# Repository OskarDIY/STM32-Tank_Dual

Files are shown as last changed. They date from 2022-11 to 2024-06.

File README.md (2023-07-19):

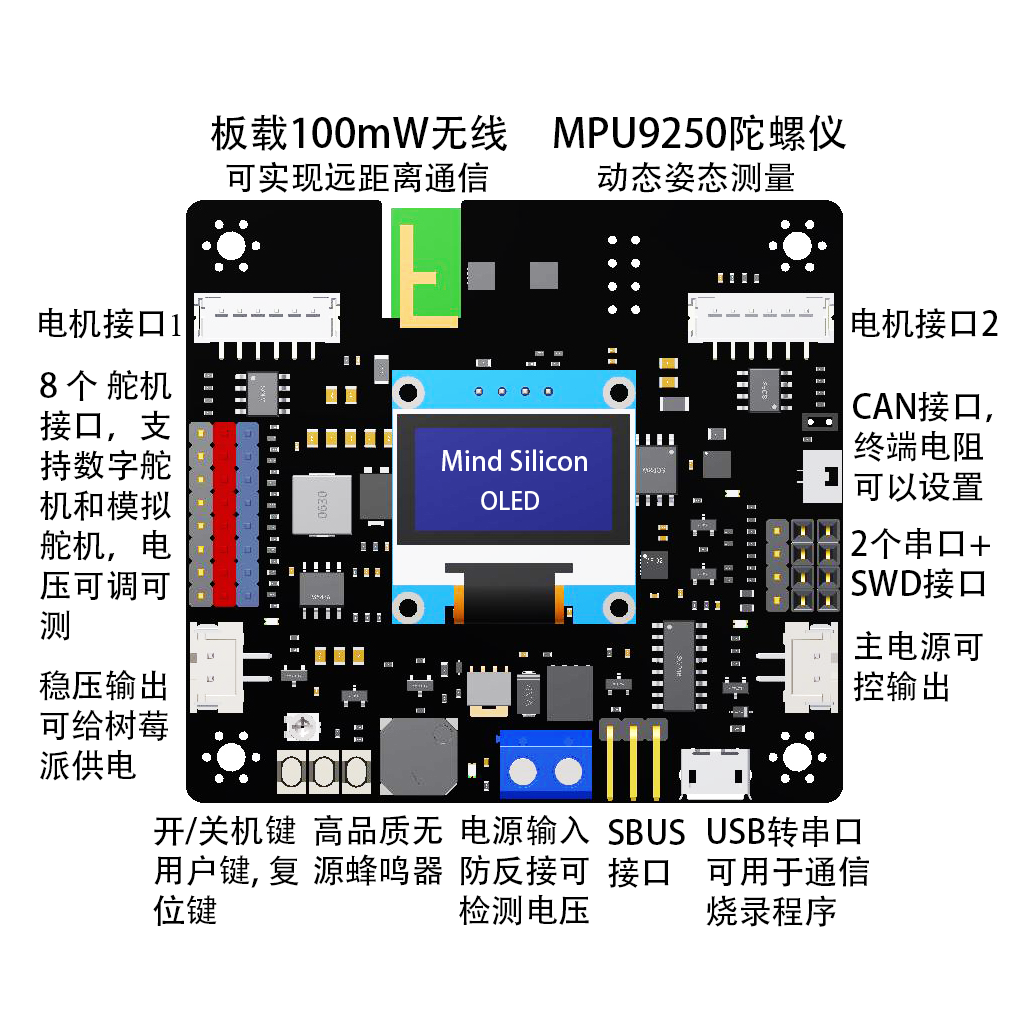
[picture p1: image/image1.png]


Tank Dual开发板是一款专门为机器人项目开发的STM32多功能控制板，可以同时控制8个舵机和2个编码电机，板载MPU9250姿态传感器，自带100mW无线可实现远距离遥控、通信，支持CAN通信，USB烧录/通信，串口通信等。稳压输出可以对外给树莓派供电，控制外部负载。  
主控：STM32F103RCT6，72MHz，ARM-Cortex M3内核，主流学习平台。  
无线：板载100mW无线模块，频段2.4GHz，可设置地址和频道。自带PCB天线距离轻松超过200米，可接外置天线距离可达500米，可本店手柄配套使用。  
9轴传感器：MPU9250（3轴陀螺仪+3轴加速度+3轴磁力计）  
舵机接口：8路硬件PWM舵机接口，5A大电流稳压芯片，可调电压。  
电机接口：2路直流有刷电机接口，支持正交编码器，每路3A大电流，支持12/24V电机。  
OLED屏幕：0.96寸OLED，可以显示信息，播放开关机动画。  
USB转串口：板载1路USB转串口电路，可以与电脑或树莓派USB通信，可以通过USB烧录程序。  
串口：2路串口（1路可以用作SBUS，与航模SBUS接收机通信）。  
CAN通信：1路CAN接口（带跳线电阻）。  
存储：板载W25Q64闪存芯片，内置文件系统，方便保存数据。  
声光提示：无源蜂鸣器，可以播放音乐，1路系统LED，3路电源LED。  
按键：开机/关机键，复位键，1个用户自定义按键。  
电源输入：6～24V供电，支持对外3A可控输出，可测量电压。  
稳压输出：支持对外3A稳压输出，与舵机共用稳压电源，开关可控，可测量电压，可以给树莓派供电。（舵机和稳压输出总和不可超过5A）。  
调试接口：SWD接口。  

说明：项目开发者在2023年5月发布了新版本的硬件，接口和外观跟原来的板子完全一致，STM32单片机的IO口分配和之前略有变化，更加优化和完善，代码和原理图也在2023年5月28日重新上传了。如果您手上用的是之前早期版本的硬件，因为硬件原理的改变，新的代码将不再适用，您可以私信开发者获取早期版本的资料，感谢您的理解！

 **项目开发工具为：STM32CubeIDE，可自行在ST官网下载安装。** 

原理图和源码的相关讲解可以在B站查看，https://space.bilibili.com/375400171/video

开发板购买链接，https://item.taobao.com/item.htm?spm=a230r.7195193.1997079397.6.b6c05627CU6ucV&id=565040857054&abbucket=20

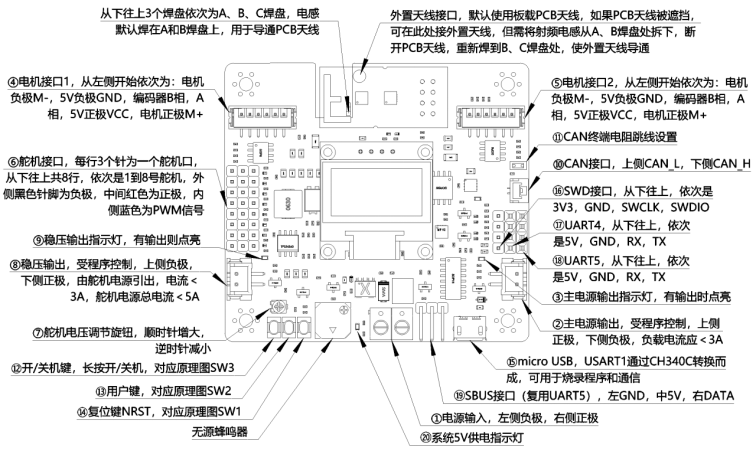
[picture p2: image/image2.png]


上图中需要注意的是：  
⑫开/关机键，长按可以开/关机，对应原理图SW3。在USB和主电源同时供电时，程序会自动运行，但仍需通过按键开机后主电源才会启动，电机和舵机才会得到电力供应。  
⑬用户键，对应原理图SW2，可通过程序来实现自定义功能。  
⑭复位键NRST，对应原理图SW1，按下后使STM32复位。程序执行异常，或者通过SWD下载程序出错时可以尝试通过复位排除问题。  
①主电源接口为整个系统的供电接口，左侧负极，右侧正极，支持2~6S电池输入。  
②主电源输出口电压与主电源接口输入电压相同，接口类型为XH2.54-2P，上侧正极，下侧负极，负载电流应＜3A，输出受程序控制。只能输出，不可用于输入。  
③主电源输出指示灯，当主电源输出口有输出时点亮。  
④⑤电机接口为PH2.0-6P接口，线序为M-、5V-、B、A、VCC、M+，在连结电机时请确保线序正确。电机驱动电压与主电源接口输入电压相同。  
⑥舵机接口，每行3个针为一个舵机口，从下往上共8行，依次是1到8号舵机，外侧黑色针脚为负极，中间红色为正极，内侧蓝色为PWM信号。为了匹配不同电压规格的舵机，舵机口的电压是可以通过⑦调节的。  
⑦电压调节旋钮，可以调节⑥舵机接口和⑧稳压输出电压，顺时针增大，逆时针减小。
⑧稳压输出接口，接口类型为XH2.54-2P，输出受程序控制，上侧负极，下侧正极。负载电流应＜3A，可以用于给树莓派供电。由于稳压输出是从舵机电源中引出，它的电压同样受⑦控制，且和舵机电源总电流应＜5A。给树莓派供电时，请务必注意使稳压输出电压≤5V，且确认好正、负极接线正确，否则将烧坏树莓派。  
⑨稳压输出指示灯，当稳压输出口有输出时点亮。  
⑩CAN接口，接口类型为GH1.25-2P，上侧CAN_L，下侧CAN_H。  
⑪CAN终端电阻跳线设置，跳线帽为2.0毫米规格。  
⑮micro USB，USART1通过CH340C转换而成，可用于烧录程序和通信。当无法通过SWD下载程序时，也可以通过USB下载程序。  
⑯SWD接口，从下往上，依次是3V3，GND，SWCLK，SWDIO。此处的3V3即3.3V，只可用于编程器烧录，不可对外供电。  
⑰UART4，从下往上，依次是5V，GND，RX，TX，此处的5V外接负载电流应＜50mA。  
⑱UART5，从下往上，依次是5V，GND，RX，TX，此处的5V外接负载电流应＜50mA。  
⑲SBUS接口（复用UART5），左GND，中5V，右DATA，此处的5V外接负载电流应＜50mA。  
⑳系统5V供电指示灯。  

2.2无线介绍  
无线发射功率100mW，频段2400 ~ 2525MHz。  
可通过上位机软件设置无线地址和频道，见下文。  

3、注意事项  
控制板可以通过SWD接口或USB接口烧录程序，SWD烧录速度快且支持调试，USB接口可以在没有编程器（ST-Link或JLink）的情况下完成烧录工作。  
SWD烧录可以直接在Keil中完成，烧录时需要通过USB供电，如果用主电源供电，则需要按住开机键不要松开。  
SWD烧录中，如果Keil提示内部异常、内部错误，一般是由于STM32没有响应编程器的复位指令，需要手动按住板子上的复位键，同时点击Keil中的下载按钮（或者按下F8），然后迅速松开复位键，程序即可下载到芯片中。  
开/关机动画保存在外置Flash芯片W25Q64中，不会因为重新烧录程序而丢失。格式化外置Flash芯片或者删除芯片中的资源文件，将导致开/关机动画丢失，但不会影响其他功能。  

4、通信协议  
4.1通信数据格式  
该通信协议适用于手柄、控制板和上位机三者之间的通信。手柄，接收机，上位机软件，受控设备之间，所有通信内容均用16进制表示，小端模式（低字节在前，高字节在后），单次通信数据长度不可超过32字节。  
格式：帧头 + 通信代码 + 帧长度 + 数据 + 校验  
其中具体含义为：  
帧头：2字节，固定为0xAAAA，用于表示一次通信的开始，或者区分不同数据帧。  
通信代码：1字节，用来区分通信的类型，详见表4.1。  
帧长度：1字节，本次通信数据帧长度，指包含帧头、通信代码、帧长度、数据和校验在内的总长度。  
数据：若干字节，数据载荷，长度可变。  
校验：16位CRC校验值，MODBUS格式。详见表4.2。  
表4.1	通信代码说明  
通信代码	说明  
0x01	遥控指令，这是一条从手柄发往接收机的指令。手柄通过这条指令将摇杆、按键、手柄电量在内的所有信息发送给接收机，接收机再通过串口输出。发送频率为200Hz。  
0x09	反馈指令，这是一条从接收机发往手柄的指令，用来触发手柄震动。用户通过接收机的串口把这条指令发送给接收机，然后接收机通过无线发送给手柄，手柄发出震动。没有发送频率限制，用户可以根据需要去触发手柄震动。  
0x15	下行透传指令，上位机通过USB把指令发送给手柄，手柄将指令发送给接收机，然后接收机通过串口输出。注意：长度不可以超过26字节。  
0x16	上位机发送指令给控制板，设置8个舵机的PWM值和电机转速值，使能稳压输出和主电源输出。此指令会启动内部PID调速算法，请确保电机霍尔编码器正常。  
0x1D	上行透传指令，用户通过接收机的串口把这条指令发送给接收机，然后接收机通过无线发送给手柄，手柄通过USB接口输出该指令。注意：长度不可以超过26字节。  

表4.2	CRC算法说明  
CRC算法	多项式公式	宽度	多项式	初始值	异或值	输入反转	输出反转  
MODBUS	x16 + x15 + x2 + 1	16	8005	0xFFFF	0x0000	true	true  
CRC算法的参考程序，见例程或校准软件。CRC16计算页面链接（注意选MODBUS算法）http://www.ip33.com/crc.html  

4.2通信示例  
0x01指令：该指令是所有指令中最重要的指令，只有理解它的含义，才可以弄清楚手柄是如何控制其他设备的。指令中所有数据均为16进制，下边给出0x01指令的具体示例：  
示例：AA AA 01 0D DF 7F 7F 7F 7F 00 00 D7 51  
第1、2字节0xAA，0xAA为帧头，标志着一帧数据的开始。  
第3字节0x01为命令代码。  
第4字节0x0D为帧长度，这条指令长度为13个字节，用16进制表示就是0x0D。  
第5字节0xDF表示手柄电池此时的电压，计算公式：（0xDF +200）÷100=4.23V，此时手柄电池电压为4.23V，其它值时以此类推。手柄低电量提醒电压为3.8V，自动关机电压为3.75V。
第6字节为模拟通道1，对应手柄左侧摇杆的水平方向，取值范围为0x00~0xFF，中值为0x7F。摇杆往左打极限值为0xFF，往右打极限值为0x00。
第7字节为模拟通道2，对应手柄左侧摇杆的垂直方向，取值范围为0x00~0xFF，中值为0x7F。摇杆往下打极限值为0xFF，往上打极限值为0x00。
第8字节为模拟通道3，对应手柄右侧摇杆的水平方向，取值范围为0x00~0xFF，中值为0x7F。摇杆往左打极限值为0xFF，往右打极限值为0x00。
第9字节为模拟通道4，对应手柄右侧摇杆的垂直方向，取值范围为0x00~0xFF，中值为0x7F。摇杆往下打极限值为0xFF，往上打极限值为0x00。
第10、11字节，这两个字总共16位，对应手柄的16个通道。从最高位第16位到第1位，依次是：L2、L1、LU、LL、LD、LR、SE、ST、RL、RD、RR、RU、R1、R2、R-KEY、L-KEY。其中R-KEY和L-KEY为摇杆往下按对应的按键。
第12、13字节为校验值，计算前11个字节的CRC16校验值得到0x51D7，按照小端模式，低字节0xD7，高字节0x51依次排列。

0x09指令：接收机发往该指令给手柄，用于触发手柄震动。
示例：AA AA 09 07 01 0E 32
第1、2字节0xAA，0xAA为帧头，标志着一帧数据的开始。
第3字节0x09为命令代码。
第4字节0x07为帧长度，这条指令长度为7个字节。
第5字节0x01表示触发手柄左侧电机振动，如果要触发邮册电机则应为0x02。该字节只能取0x01或者0x02。
第6、7字节为校验值，计算前5个字节的CRC16校验值得到0x320E，按照小端模式，低字节0x0E，高字节0x32依次排列。

0x15指令：上位机通过手柄透传给接收机的数据，然后通过接收机输出给STM32进行处理。
示例：AA AA 15 07 00 0E 34
第1、2字节0xAA，0xAA为帧头，标志着一帧数据的开始。
第3字节0x15为命令代码。
第4字节0x07为帧长度，这条指令长度为7个字节。
第5字节0x00上位机发出的数据，字节长度可变，但不可超过26字节。因为一次通信最多发送32字节数据，其他部分已占据6字节。
第6、7字节为校验值，计算前5个字节的CRC16校验值得到0x340E，按照小端模式，低字节0x0E，高字节0x34依次排列。
可以通过这条指令来模拟手柄向开发板发送的数据，格式参照0x01指令。可以用于实现上位机通过控制板的USB口向控制板发送指令数据，控制板像响应手柄指令一样做出相同响应，具体实现由用户决定。

0x16指令：上位机发送指令给控制板，设置8个舵机的PWM值和电机转速值，启动稳压输出和主电源输出。PWM有效范围是500~2500μS，PWM频率为50Hz。每个电机的转速值用2个字节（BYTE1，BYTE2，简写为B1、B2）表示。B1字节的最高2位用来表示：惯性滑行（00）、正转（01）、反转（10）、阻尼刹车（11）。B1字节低6位和B2字节8位共同组成速度值(((B1 & 0x3F)<< 8) | B2)。当B1高2位为正转（01）或者反转（10）时，如果速度值为0则会锁定电机位置，使电机迅速停转并保持不动。电机速度的单位为毫米每秒（mm/s），表示电机转动所产生的线速度。
示例：AA AA 16 1B 00 00 00 00 00 00 00 00 00 00 00 00 00 00 00 00 00 00 00 00 00 5E A6
             舵机：1    2    3    4    5    6    7    8   B1B2 B1B2 PWR
第1、2字节0xAA，0xAA为帧头，标志着一帧数据的开始。
第3字节0x15为命令代码。
第4字节0x1B为帧长度，这条指令长度为27个字节，即十六进制0x1B。
第5 ~ 20字节依次为1至8舵机口的PWM值，每个舵机占用2个字节，注意PWM有效范围是500~2500μS，PWM频率为50Hz。
第21~24字节依次为电机1接口和电机2接口的转速值。每个电机的转速值用2个字节（BYTE1，BYTE2，简写为B1、B2）表示。B1字节的最高2位用来表示：惯性滑行（00）、正转（01）、反转（10）、阻尼刹车（11）。B1字节低6位和B2字节8位共同组成速度值(((B1 & 0x3F)<< 8) | B2)。当B1高2位为正转（01）或者反转（10）时，如果速度值为0则会锁定电机位置，使电机迅速停转并保持不动。电机速度的单位为毫米每秒（mm/s），表示电机转动所产生的线速度。
直流减速电机转速一般在1000RPM（转每分钟）以内，根据电机转速和车轮直径可以算出车轮线速度的合理区间。请注意输入合理的速度值，以免电机过载。需要特别注意的是，此指令会启动内部PID调速算法，请确保电机编码器正常，编码器异常可能导致灾难性后果。
第25字节PWR用于启动稳压输出和主电源输出，0x00表示不启动，0x01表示仅启动舵机电源用于对外提供稳压供电，0x02表示仅启动主电源输出口对外供电，0x03表示同时启动多机电源和主电源。注意启动前务必检查舵机电源和主电源电压，以免烧坏外接设备。另外，请确保系统主电源已经接通且开启，参考2.1章节接开关机操作。
第26、27字节为校验值，计算前25个字节的CRC16校验值得到0xA65E，按照小端模式，低字节0x5E，高字节0xA6依次排列。

0x1E指令：控制板对上位机0x16指令的返回信息，用来返回设置是否成功，以及电机转速、设备姿态、故障信息。
示例：AA AA 1E 11 00 00 00 00 00 00 00 00 00 00 00 7F F6
B1B2 B1B2  R    P    Y
第1、2字节0xAA，0xAA为帧头，标志着一帧数据的开始。
第3字节0x1E为命令代码。
第4字节0x11为帧长度，这条指令长度为17个字节。
第5字节0x00表示设置完成，0x1表示霍尔故障，0x02表示电机过载，0x03表示因为即将接触障碍物而触发制动，0x04表示因为即将跌落而触发制动。
第6~9字节依次为电机1接口和电机2接口的转速值。每个电机的转速值用2个字节（BYTE1，BYTE2，简写为B1、B2）表示。B1字节的最高2位用来表示：惯性滑行（00）、正转（01）、反转（10）、阻尼刹车（11）。B1字节低6位和B2字节8位共同组成速度值(((B1 & 0x3F)<< 8) | B2)。当B1高2位为正转（01）或者反转（10）时，如果速度值为0则会锁定电机位置，使电机迅速停转并保持不动。电机速度的单位为毫米每秒（mm/s），表示电机转动所产生的线速度。
第10~15字节依次为姿态数据：横滚角Roll、俯仰角Pitch、偏航角Yaw，每个角度包含2个字节（16位有符号整型，小端模式），需要除以10才是实际角度值。比如Roll值为0x7A，换算成十进制为122，那么实际Roll角度为12.2°。
第16、17字节为校验值，计算前5个字节的CRC16校验值得到0xF67F，按照小端模式，低字节0x7F，高字节0xF6依次排列。

0x17指令：读取控制板信息，包括8个舵机的PWM值和电机转速值，稳压输出状态和主电源输出状态，舵机电压（同稳压输出电压）和主电源电压。
示例：AA AA 17 06 8E 2E
第1、2字节0xAA，0xAA为帧头，标志着一帧数据的开始。
第3字节0x17为命令代码。
第4字节0x06为帧长度，这条指令长度为6个字节。
第5、6字节为校验值，计算前4个字节的CRC16校验值得到0x2E8E，按照小端模式，低字节0x8E，高字节0x2E依次排列。

0x1F指令：对0x17指令的响应，用于返回控制板信息，其中包括8个舵机的PWM值和电机转速值，稳压输出状态和主电源输出状态，舵机电压（同稳压输出电压）和主电源电压。
示例：AA AA 1F 1D 00 00 00 00 00 00 00 00 00 00 00 00 00 00 00 00 00 00 00 00 00 00 00 8D 16
             舵机：1    2    3    4    5    6    7    8   B1B2 B1B2 PWR
第1、2字节0xAA，0xAA为帧头，标志着一帧数据的开始。
第3字节0x1F为命令代码。
第4字节0x1D为帧长度，这条指令长度为29个字节。
第5 ~ 20字节依次为1至8舵机口的PWM值，每个舵机占用2个字节，注意PWM有效范围是500~2500μS，PWM频率为50Hz。注意数据格式为小端模式（低字节在前，高字节在后），比PWM值1500用十六进制表示为0x05DC，发送顺序为先发0xDC，后发0x05。
第5 ~ 20字节依次为1至8舵机口的PWM值，每个舵机占用2个字节，注意PWM有效范围是500~2500μS，PWM频率为50Hz。
第21~24字节依次为电机1接口和电机2接口的转速值。每个电机的转速值用2个字节（BYTE1，BYTE2，简写为B1、B2）表示。B1字节的最高2位用来表示：惯性滑行（00）、正转（01）、反转（10）、阻尼刹车（11）。B1字节低6位和B2字节8位共同组成速度值(((B1 & 0x3F)<< 8) | B2)。当B1高2位为正转（01）或者反转（10）时，如果速度值为0则会锁定电机位置，使电机迅速停转并保持不动。电机速度的单位为毫米每秒（mm/s），表示电机转动所产生的线速度。
第25字节PWR用于启动稳压输出和主电源输出，0x00表示不启动，0x01表示仅启动舵机电源用于对外提供稳压供电，0x02表示仅启动主电源输出口对外供电，0x03表示同时启动多机电源和主电源。注意启动前务必检查舵机电源和主电源电压，以免烧坏外接设备。另外，请确保系统主电源已经接通且开启，参考2.1章节接开关机操作。
第26、27字节，分别表示舵机电源（同稳压电源）的电压和主电源电压，取值为正数，需要除以10才是实际电压。比如电压值为0x7A，换算成十进制为122，那么实际电压为12.2V。
第28、29字节为校验值，计算前27个字节的CRC16校验值得到0x168D，按照小端模式，低字节0x8D，高字节0x16依次排列。

0x1D指令：STM32把这条指令发送给接收机，然后接收机通过无线发送给手柄，手柄通过USB口输出给上位机。
示例：AA AA 1D 07 00 8F F6
第1、2字节0xAA，0xAA为帧头，标志着一帧数据的开始。
第3字节0x1D为命令代码。
第4字节0x07为帧长度，这条指令长度为7个字节。
第5字节0x00接收机透传给上位机的数据，字节长度可变，但不可超过26字节。因为一次通信最多发送32字节数据，其他部分已占据6字节。
第6、7字节为校验值，计算前5个字节的CRC16校验值得到0xF68F，按照小端模式，低字节0x8F，高字节0xF6依次排列。

5、设置  
手柄和接收机在出厂前已完成配对和校准。无线地址由5个字节组成，出厂默认地址为0x11，0x22，0x33，0x44，0x55，默认频率为2400MHz。  
如果要修改地址和频率，请先在www.mindsilicon.com下载手柄配置软件（仅限windows系统）。请先将接收机设置到目标地址和频率，然后把手柄设置到相同的地址和频率，重启手柄和接收机，即可完成配对。  

5.1无线设置  
请先将开发板通过USB连接到电脑上，确认电脑已经安装过CH340驱动程序，驱动安装见后边章节。  
然后打开配置软件，如下图所示。选择接收机所对应的串口，点击“打开串口”，点击“读取配置”可以读取接收机的地址和频率。在下拉框中可以选择要设定的地址和频率，点击“写入频率”和“写入地址”完成配置。重启接收机即可生效配置。  
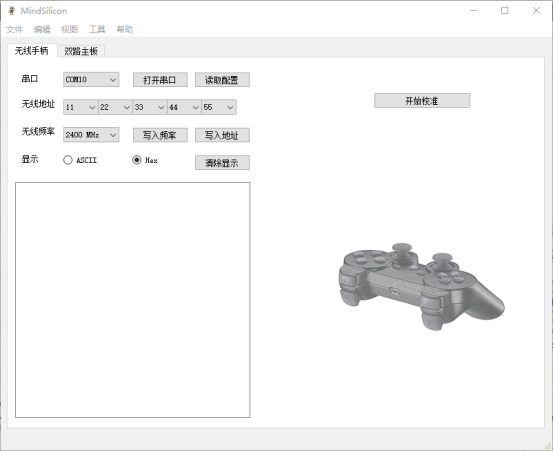
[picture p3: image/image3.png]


5.2手柄设置  
手柄的无线地址和频率设置与接收机相同，可以参考上边步骤，重启手柄后新的无线设置即可生效。接收机摇杆可以通过上边的软件进行校准。  

6、USB烧录  
固件升级软件和驱动程序，可以在www.mindsilicon.com下载（仅限windows系统）。  

6.1驱动安装  
双击CH341SER.EXE启动安装程序  

输入图片说明

选择安装，等待安装完成。

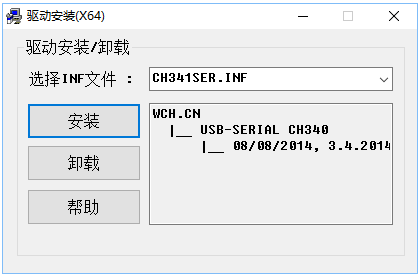
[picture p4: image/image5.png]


驱动安装成功后，在设备管理器可以看到会有一个端口出现。  

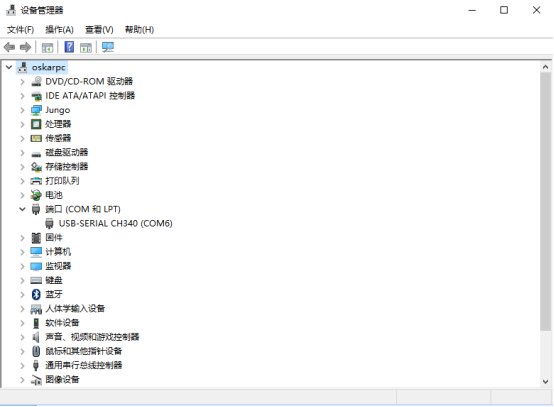
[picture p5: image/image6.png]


如果驱动已经安装过，但对应端口旁有叹号提示，可以右击更新驱动，然后浏览已经安装好的驱动，选择正确驱动即可，如下图。  

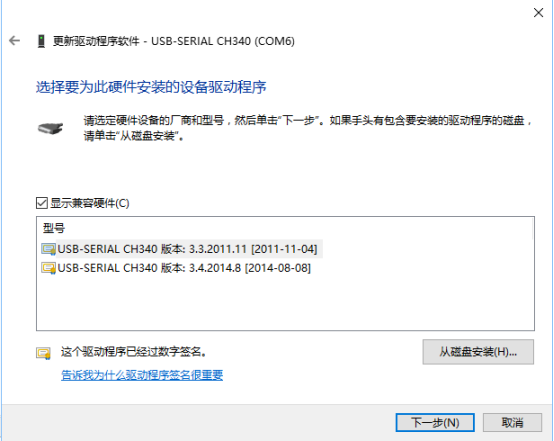
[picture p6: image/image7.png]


6.2烧录固件  

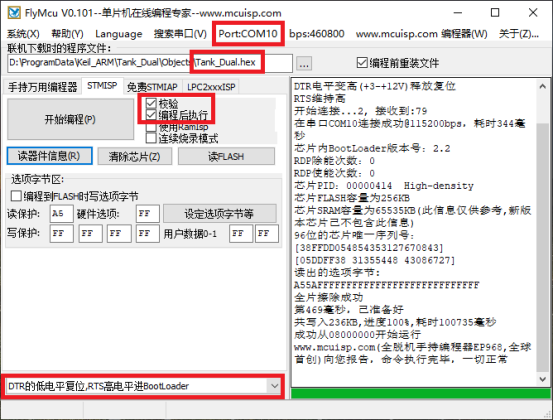
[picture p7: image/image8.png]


操作流程：  
1、用miniUSB线将手柄连接到电脑上，选择正确的端口，这里是COM10，波特率115200.如果不确定是哪个端口，可以打开设备管理器查看。如果没有找到对应端口，请检查驱动程序是否安装正确，驱动安装见上一章节。  
2、浏览到需要升级的固件（hex）文件。  
3、选择STMISP，然后勾选“校验”和“编程后执行”。  
4、选择“DTR的低电平复位，RTS高电平进BootLoader”。  
5、用手按住手柄上的电源键“P3键”不要松开，点击“开始编程”，直到程序下载完成。  
控制板升级固件后，无线配置全部恢复默认设置。  

7、尺寸说明  

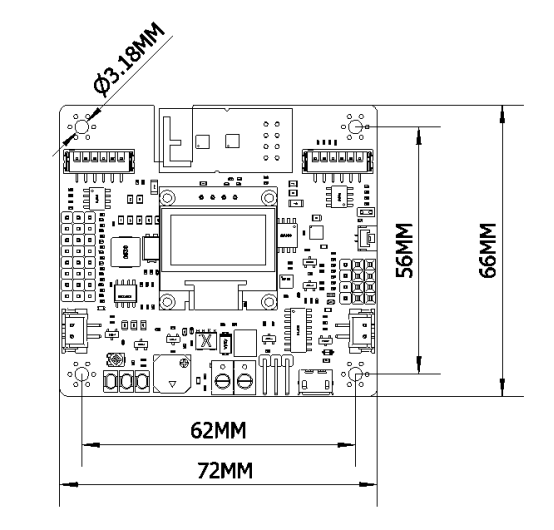
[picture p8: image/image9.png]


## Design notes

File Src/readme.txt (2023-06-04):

// 处理无线数据
void ParseRadioMsg(radioMsg_t *msg)
{
	int16_t pwm1 = 0, pwm2 = 0;
	static float duty[8] = {0.5, 0.5, 0.5, 0.5, 0.5, 0.5, 0.5, 0.5};
	uint16_t keys = 0;
	
	// 先计算电机的PWM值, data[4]是右侧摇杆垂直方向, 用来控制前后运动
	pwm1 = -(msg->data[4] - 0x7F) * 8;
	pwm2 = pwm1;
	// data[3]是右侧摇杆水平方向, 用来控制左右转向时电机的差速
	pwm1 += (msg->data[3] - 0x7F) * 5;
	pwm2 -= (msg->data[3] - 0x7F) * 5;
	motorStatus.motor1_pwm = pwm1;
	motorStatus.motor2_pwm = pwm2;
	
	// data的第6和第7字节, 这两个字节共16位, 对应手柄的16个通道, 
	// 从最高位第16位到第1位, 依次是：L2, L1, LU, LL, LD, LR, SE,
	// ST, RL, RD, RR, RU, R1, R2, R-KEY, L-KEY
	// 其中R-KEY和L-KEY分别是左右摇杆向下按下对应的按键
	keys = (msg->data[5] << 8) | msg->data[6];
	
	// 2号舵机控制, 用L1和R1键控制正转和反转, 
	if((keys & (1 << 14)) && (!(keys & (1 << 3))))				// L1按下且R1松开时
	{
		duty[1] -= 0.005;
		PWM(&duty[1]);
		servoPWM.servo2 = Duty_to_PWM(duty[1]);
	}
	else if((!(keys & (1 << 14))) && (keys & (1 << 3)))		// L1松开且R1按下时
	{
		duty[1] += 0.005;
		PWM(&duty[1]);
		servoPWM.servo2 = Duty_to_PWM(duty[1]);
	}
	
	// 3号舵机控制, 用L2和R2键控制正转和反转, 
	if((keys & (1 << 15)) && (!(keys & (1 << 2))))				// L2按下且R2松开时
	{
		duty[2] -= 0.005;
		PWM(&duty[2]);
		if(duty[2] < 0.1)		// 防止云台垂直舵机转动角度过大，而导致堵转
		{
			duty[2] = 0.1;
		}
		servoPWM.servo3 = Duty_to_PWM(duty[2]);
	}
	else if((!(keys & (1 << 15))) && (keys & (1 << 2)))		// L2松开且R2按下时
	{
		duty[2] += 0.005;
		PWM(&duty[2]);
		if(duty[2] > 0.9)		// 防止云台垂直舵机转动角度过大，而导致堵转
		{
			duty[2] = 0.9;
		}
		servoPWM.servo3 = Duty_to_PWM(duty[2]);
	}
}

// 显示系统参数 
void OLED_ShowParm(void)
{
	char volt1[20],volt2[20],motor1[20],motor2[20];
	
	sprintf(volt2,"Main  Voltage:%5.2f",ADC_ConvertedValueLocal[1]);
	OLED_ShowStr(0,0,(uint8_t*)(&volt2),1);
	
	sprintf(volt1, "Servo Voltage:%5.2f",ADC_ConvertedValueLocal[0]);
	OLED_ShowStr(0,1,(uint8_t*)(&volt1),1);
	
	sprintf(motor1,"motor1_pwm:%5d",motorStatus.motor1_pwm);
	OLED_ShowStr(0,4,(uint8_t*)(&motor1),1);
	
	sprintf(motor2,"motor2_pwm:%5d",motorStatus.motor2_pwm);
	OLED_ShowStr(0,5,(uint8_t*)(&motor2),1);
	
	vTaskDelay(50);	
}

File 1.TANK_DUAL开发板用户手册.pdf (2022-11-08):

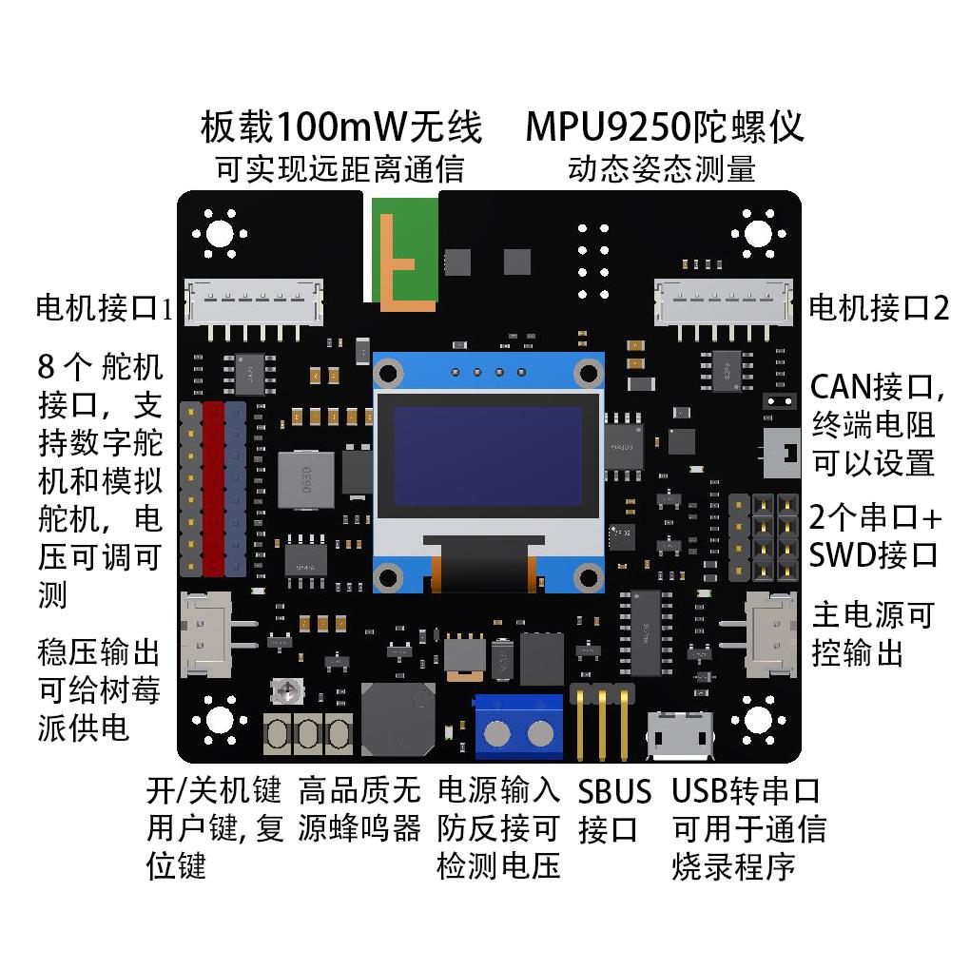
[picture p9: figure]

www.mindsilicon.com | v1.0
Mind Silicon | 用户手册

# TANK_DUAL 开发板

## 用户手册

## Important Notice

### Mind Silicon products are neither intended nor warranted for usage in systems or equipment, any malfunction or failure of which may cause loss of human life, bodily

injury or severe property damage. Such applications are deemed, “Insecure Usage”. Insecure usage includes, but is not limited to: equipment for surgical implementation, atomic energy control instruments, airplane or spaceship instruments, the control or

### operation of dynamic, brake or safety systems designed for vehicular use, traffic

### signal instruments, all types of safety devices, and other applications intended to

support or sustain life. All Insecure Usage shall be made at customer’s risk, and in the event that third parties

### lay claims to Mind Silicon as a result of customer’s Insecure Usage, customer shall

indemnity the damages and liabilities thus incurred by Mind Silicon. ©2020 Mind Silicon Technologies all rights reserved. Reproduction in whole or in

### part is prohibited without the prior written permission of the copyright holder. 免责声明

感谢您购买使用该产品，在使用之前，请仔细阅读本声明，一旦使用，即被视为对本声明全

部内容的认可和接受。请严格遵守手册、产品说明和相关法律法规、政策、准则安装和使用

该产品。在使用产品过程中，用户承诺对自己的行为以及因此而产生的所有后果负责。因用

户不当使用、安装、改装造成的任何损失，我方将不承担法律责任。

该产品禁止在任何因故障或失效可能导致人员伤亡、人身伤害或者财产损失的系统或设备中

使用，此类使用被视为“不安全使用”，所有不安全使用造成的任何损失由用户承担。不安全

使用包括但不限于：用于外科手术的设备，原子能控制设备，飞机或宇宙飞船仪器，车辆的

动力控制，制动或安全系统，交通信号设备，所有类型的安全装置以及旨在支持或维持生命

的其他应用。

关于免责声明的最终解释权，归 Mind Silicon 所有。

©2020 Mind Silicon Technologies 保留所有权利。未经版权所有者的事先书面许可，禁止全

部或部分复制。

目录

### 1、产品特性

Tank Dual 开发板是一款专门为机器人项目开发的 STM32 多功能控制板，可以同时控制 8

个舵机和 2 个编码电机，板载 MPU9250 姿态传感器，自带 100mW 无线可实现远距离遥控、

通信，支持 CAN 通信，USB 烧录/通信，串口通信等。稳压输出可以对外给树莓派供电，

控制外部负载。

- 主控：STM32F103RCT6，72MHz，ARM-Cortex M3 内核，主流学习平台。
- 无线：板载 100mW 无线模块，频段 2.4GHz，可设置地址和频道。自带 PCB 天线距离

轻松超过 200 米，可接外置天线距离可达 500 米，可本店手柄配套使用。

- 9 轴传感器：MPU9250（3 轴陀螺仪+3 轴加速度+3 轴磁力计）
- 舵机接口：8 路硬件 PWM 舵机接口，5A 大电流稳压芯片，可调电压。
- 电机接口：2 路直流有刷电机接口，支持正交编码器，每路 3A 大电流，支持 12/24V 电

机。

- OLED 屏幕：0.96 寸 OLED，可以显示信息，播放开关机动画。
- USB 转串口：板载 1 路 USB 转串口电路，可以与电脑或树莓派 USB 通信，可以通过

USB 烧录程序。

- 串口：2 路串口（1 路可以用作 SBUS，与航模 SBUS 接收机通信）。
- CAN 通信：1 路 CAN 接口（带跳线电阻）。
- 存储：板载 W25Q64 闪存芯片，内置文件系统，方便保存数据。
- 声光提示：无源蜂鸣器，可以播放音乐，1 路系统 LED，3 路电源 LED。
- 按键：开机/关机键，复位键，1 个用户自定义按键。
- 电源输入：6～24V 供电，支持对外 3A 可控输出，可测量电压。
- 稳压输出：支持对外 3A 稳压输出，与舵机共用稳压电源，开关可控，可测量电压，可

以给树莓派供电。（舵机和稳压输出总和不可超过 5A）。

- 调试接口：SWD 接口。

### 2、功能介绍

### 2.1 接口说明

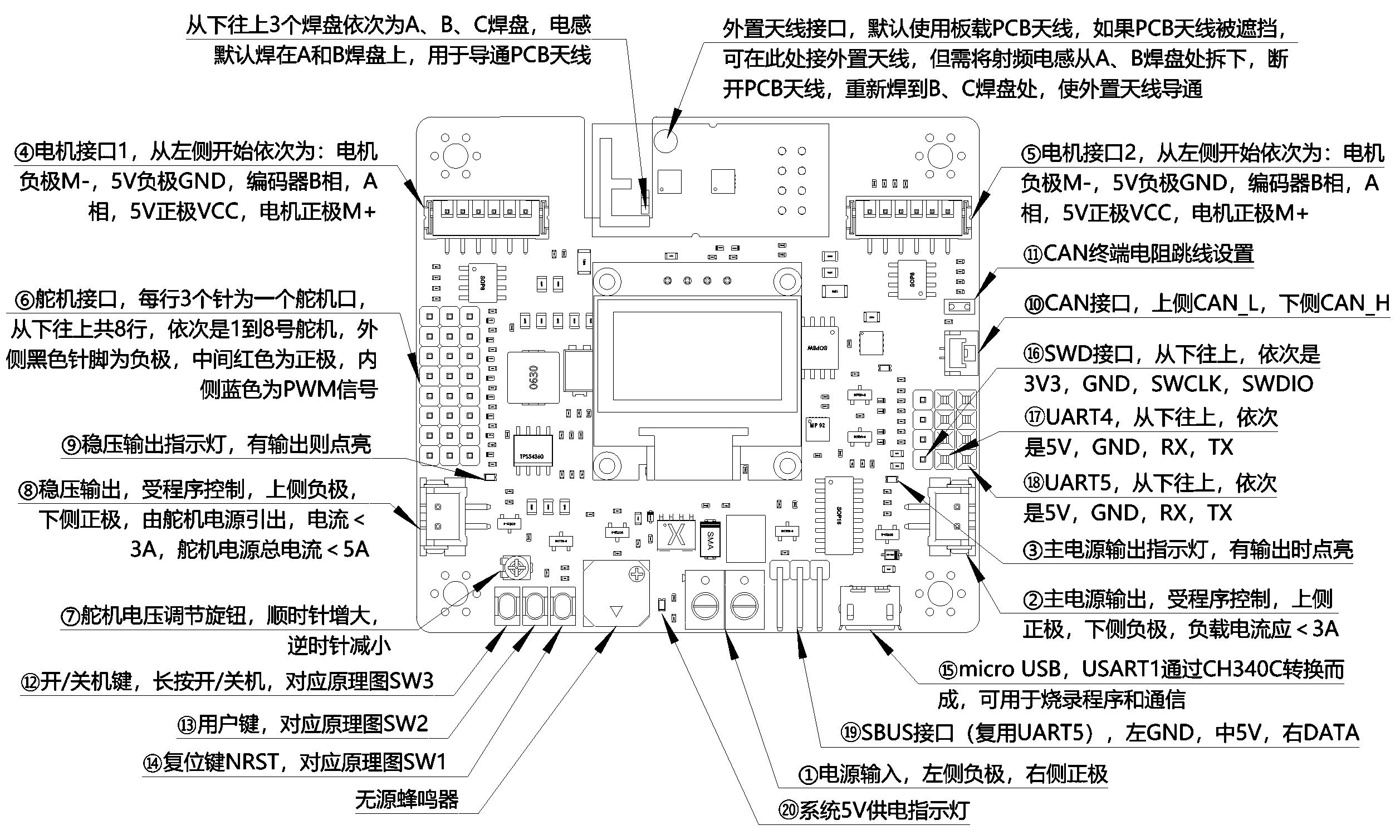
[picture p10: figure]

上图中需要注意的是：

- ⑫开/关机键，长按可以开/关机，对应原理图 SW3。在 USB 和主电源同时供电时，程

序会自动运行，但仍需通过按键开机后主电源才会启动，电机和舵机才会得到电力供应。

- ⑬用户键，对应原理图 SW2，可通过程序来实现自定义功能。
- ⑭复位键 NRST，对应原理图 SW1，按下后使 STM32 复位。程序执行异常，或者通过

SWD 下载程序出错时可以尝试通过复位排除问题。

- ①主电源接口为整个系统的供电接口，左侧负极，右侧正极，支持 2~6S 电池输入。
- ②主电源输出口电压与主电源接口输入电压相同，接口类型为 XH2.54-2P，上侧正极，

下侧负极，负载电流应＜3A，输出受程序控制。只能输出，不可用于输入。

- ③主电源输出指示灯，当主电源输出口有输出时点亮。
- ④⑤电机接口为 PH2.0-6P 接口，线序为 M-、5V-、B、A、VCC、M+，在连结电机时

请确保线序正确。电机驱动电压与主电源接口输入电压相同。、

- ⑥舵机接口，每行 3 个针为一个舵机口，从下往上共 8 行，依次是 1 到 8 号舵机，外侧

黑色针脚为负极，中间红色为正极，内侧蓝色为 PWM 信号。为了匹配不同电压规格的

舵机，舵机口的电压是可以通过⑦调节的。

- ⑦电压调节旋钮，可以调节⑥舵机接口和⑧稳压输出电压，顺时针增大，逆时针减小。
- ⑧稳压输出接口，接口类型为 XH2.54-2P，输出受程序控制，上侧负极，下侧正极。负

载电流应＜3A，可以用于给树莓派供电。由于稳压输出是从舵机电源中引出，它的电

压同样受⑦控制，且和舵机电源总电流应＜5A。给树莓派供电时，请务必注意使稳压

输出电压≤5V，且确认好正、负极接线正确，否则将烧坏树莓派。

- ⑨稳压输出指示灯，当稳压输出口有输出时点亮。
- ⑩CAN 接口，接口类型为 GH1.25-2P，上侧 CAN_L，下侧 CAN_H。
- ⑪CAN 终端电阻跳线设置，跳线帽为 2.0 毫米规格。
- ⑮micro USB，USART1 通过 CH340C 转换而成，可用于烧录程序和通信。当无法通过

SWD 下载程序时，也可以通过 USB 下载程序。

- ⑯SWD 接口，从下往上，依次是 3V3，GND，SWCLK，SWDIO。此处的 3V3 即 3.3V，

只可用于编程器烧录，不可对外供电。

- ⑰UART4，从下往上，依次是 5V，GND，RX，TX，此处的 5V 外接负载电流应＜50mA。
- ⑱UART5，从下往上，依次是 5V，GND，RX，TX，此处的 5V 外接负载电流应＜50mA。
- ⑲SBUS 接口（复用 UART5），左 GND，中 5V，右 DATA，此处的 5V 外接负载电流

应＜50mA。

- ⑳系统 5V 供电指示灯。

### 2.2 无线介绍

- 无线发射功率 100mW，频段 2400 ~ 2525MHz。
- 可通过上位机软件设置无线地址和频道，见下文。

### 3、注意事项

- 控制板可以通过 SWD 接口或 USB 接口烧录程序，SWD 烧录速度快且支持调试，USB

接口可以在没有编程器（ST-Link 或 JLink）的情况下完成烧录工作。

- SWD 烧录可以直接在 Keil 中完成，烧录时需要通过 USB 供电，如果用主电源供电，

则需要按住开机键不要松开。

- SWD 烧录中，如果 Keil 提示内部异常、内部错误，一般是由于 STM32 没有响应编程

器的复位指令，需要手动按住板子上的复位键，同时点击 Keil 中的下载按钮（或者按

下 F8），然后迅速松开复位键，程序即可下载到芯片中。

- 开/关机动画保存在外置 Flash 芯片 W25Q64 中，不会因为重新烧录程序而丢失。格式

化外置 Flash 芯片或者删除芯片中的资源文件，将导致开/关机动画丢失，但不会影响其

他功能。

### 4、通信协议

### 4.1 通信数据格式

该通信协议适用于手柄、控制板和上位机三者之间的通信，可以由上位机通过控制板的 USB

口向控制板发送此通信数据，控制板会像响应手柄指令一样做出相同响应。

手柄，接收机，上位机软件，受控设备之间，所有通信内容均用 16 进制表示，单次通信数

据长度不可超过 32 字节。

格式：帧头 + 通信代码 + 帧长度 + 数据 + 校验

其中具体含义为：

- 帧头：2 字节，固定为 0xAAAA，用于表示一次通信的开始，或者区分不同数据帧。
- 通信代码：1 字节，用来区分通信的类型，详见表 4.1。
- 帧长度：1 字节，本次通信数据帧长度，指包含帧头、通信代码、帧长度、数据和校验

在内的总长度。

- 数据：若干字节，数据载荷，长度可变。
- 校验：16 位 CRC 校验值，MODBUS 格式。详见表 4.2。

表 4.1 通信代码说明

通信代码 | 说明
0x01 | 遥控指令，这是一条从手柄发往接收机的指令。手柄通过这条指令将摇杆、按 键、手柄电量在内的所有信息发送给接收机，接收机再通过串口输出。发送频 率为 50Hz。
0x09 | 反馈指令，这是一条从接收机发往手柄的指令，用来触发手柄震动。用户通过 接收机的串口把这条指令发送给接收机，然后接收机通过无线发送给手柄，手 柄发出震动。没有发送频率限制，用户可以根据需要去触发手柄震动。
0x15 | 下行透传指令，上位机通过 USB 把指令发送给手柄，手柄将指令发送给接收 机，然后接收机通过串口输出。注意：长度不可以超过 26 字节。

0x1D

上行透传指令，用户通过接收机的串口把这条指令发送给接收机，然后接收机

通过无线发送给手柄，手柄通过 USB 接口输出该指令。注意：长度不可以超

过 26 字节。

表 4.2 CRC 算法说明

CRC 算法 | 多项式公式 | 宽度 | 多项式 | 初始值 | 异或值 | 输入反转 | 输出反转
MODBUS | x16 + x15 + x2 + 1 | 16 | 8005 | 0xFFFF | 0x0000 | true | true

CRC 算法的参考程序，见例程或校准软件。

### 4.2 通信示例

0x01 指令：该指令是所有指令中最重要的指令，只有理解它的含义，才可以弄清楚手柄是

如何控制其他设备的。指令中所有数据均为 16 进制，下边给出 0x01 指令的具体示例：

示例：AA AA 01 0D DF 7F 7F 7F 7F 00 00 D7 51

第 1、2 字节 0xAA，0xAA 为帧头，标志着一帧数据的开始。

第 3 字节 0x01 为命令代码。

第 4 字节 0x0D 为帧长度，这条指令长度为 13 个字节，用 16 进制表示就是 0x0D。

第 5 字节 0xDF 表示手柄电池此时的电压，计算公式：（0xDF +200）÷100=4.23V，此时手

柄电池电压为 4.23V，其它值时以此类推。手柄低电量提醒电压为 3.8V，自动关机电压为

3.75V。

第 6 字节为模拟通道 1，对应手柄左侧摇杆的水平方向，取值范围为 0x00~0xFF，中值为 0x7F。

摇杆往左打极限值为 0xFF，往右打极限值为 0x00。

第 7 字节为模拟通道 2，对应手柄左侧摇杆的垂直方向，取值范围为 0x00~0xFF，中值为 0x7F。

摇杆往下打极限值为 0xFF，往上打极限值为 0x00。

第 8 字节为模拟通道 3，对应手柄右侧摇杆的水平方向，取值范围为 0x00~0xFF，中值为 0x7F。

摇杆往左打极限值为 0xFF，往右打极限值为 0x00。

第 9 字节为模拟通道 4，对应手柄右侧摇杆的垂直方向，取值范围为 0x00~0xFF，中值为 0x7F。

摇杆往下打极限值为 0xFF，往上打极限值为 0x00。

第 10、11 字节，这两个字总共 16 位，对应手柄的 16 个通道。从最高位第 16 位到第 1 位，

依次是：L2、L1、LU、LL、LD、LR、SE、ST、RL、RD、RR、RU、R1、R2、R-KEY、

L-KEY。其中 R-KEY 和 L-KEY 为摇杆往下按对应的按键。

第 12、13 字节为校验值，计算前 11 个字节的 CRC16 校验值得到 0x51D7，按照小端模式，

低字节 0xD7，高字节 0x51 依次排列。

0x09 指令：接收机发往该指令给手柄，用于触发手柄震动。

示例：AA AA 09 07 01 0E 32

第 1、2 字节 0xAA，0xA 为帧头，标志着一帧数据的开始。

第 3 字节 0x09 为命令代码。

第 4 字节 0x07 为帧长度，这条指令长度为 7 个字节。

第 5 字节 0x01 表示触发手柄左侧电机振动，如果要触发邮册电机则应为 0x02。该字节只能

取 0x01 或者 0x02。

第 6、7 字节为校验值，计算前 5 个字节的 CRC16 校验值得到 0x320E，按照小端模式，低

字节 0x32，高字节 0x0E 依次排列。

0x15 指令：上位机通过手柄透传给接收机的数据，然后通过接收机的串口输出。

示例：AA AA 15 07 00 0E 34

第 1、2 字节 0xAA，0xA 为帧头，标志着一帧数据的开始。

第 3 字节 0x15 为命令代码。

第 4 字节 0x07 为帧长度，这条指令长度为 7 个字节。

第 5 字节 0x00 上位机发出的数据，字节长度可变，但不可超过 26 字节。因为一次通信最多

发送 32 字节数据，其他部分已占据 6 字节。

第 6、7 字节为校验值，计算前 5 个字节的 CRC16 校验值得到 0x340E，按照小端模式，低

字节 0x34，高字节 0x0E 依次排列。

0x1D 指令：用户通过接收机的串口把这条指令发送给接收机，然后接收机通过无线发送给

手柄，手柄通过 USB 口输出给上位机。

示例：AA AA 1D 07 00 8F F6

第 1、2 字节 0xAA，0xA 为帧头，标志着一帧数据的开始。

第 3 字节 0x1D 为命令代码。

第 4 字节 0x07 为帧长度，这条指令长度为 7 个字节。

第 5 字节 0x00 接收机透传给上位机的数据，字节长度可变，但不可超过 26 字节。因为一次

通信最多发送 32 字节数据，其他部分已占据 6 字节。

第 6、7 字节为校验值，计算前 5 个字节的 CRC16 校验值得到 0xF68F，按照小端模式，低

字节 0x8F，高字节 0xF6 依次排列。

### 5、设置和校准

手柄和接收机在出厂前已完成配对和校准。无线地址由 5 个字节组成，出厂默认地址为 0x11，

0x22，0x33，0x44，0x55，默认频率为 2400MHz。

如果要修改地址和频率，请先在 www.mindsilicon.com 下载手柄配置软件（仅限 windows 系

统）。请先将接收机设置到目标地址和频率，然后把手柄设置到相同的地址和频率，重启手

柄和接收机，即可完成配对。

### 5.1 无线设置

请先将开发板通过 USB 连接到电脑上，确认电脑已经安装过 CH340 驱动程序，驱动安装见

后边章节。

然后打开配置软件，如下图所示。选择接收机所对应的串口，点击“打开串口”，点击“读取

配置”可以读取接收机的地址和频率。在下拉框中可以选择要设定的地址和频率，点击“写入

频率”和“写入地址”完成配置。重启接收机即可生效配置。

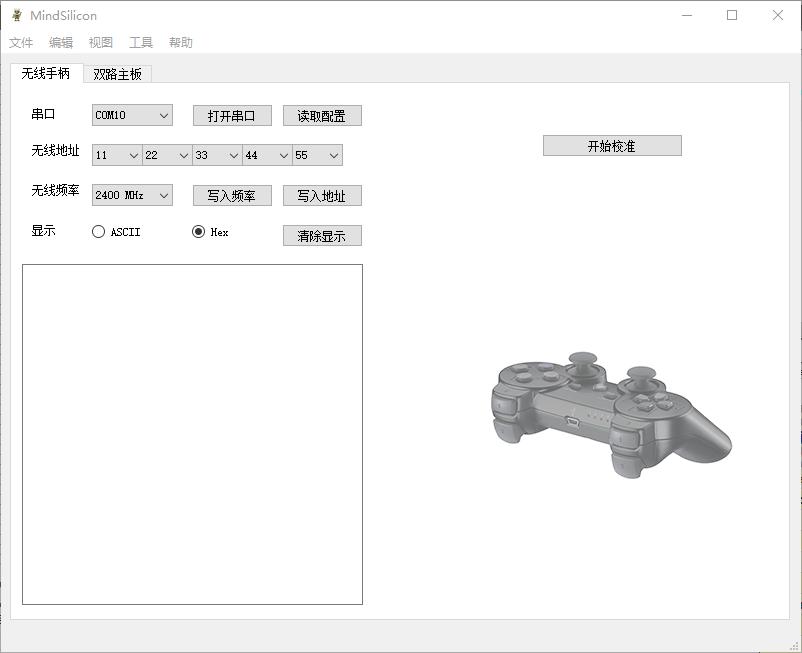
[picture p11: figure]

### 5.2 手柄设置

手柄的无线地址和频率设置与接收机相同，可以参考上边步骤，重启手柄后新的无线设置即

可生效。接收机摇杆可以通过上边的软件进行校准。

## 6、USB 烧录

固件升级软件和驱动程序，可以在 www.mindsilicon.com 下载（仅限 windows 系统）。

### 6.1 驱动安装

双击 CH341SER.EXE 启动安装程序

选择安装，等待安装完成。

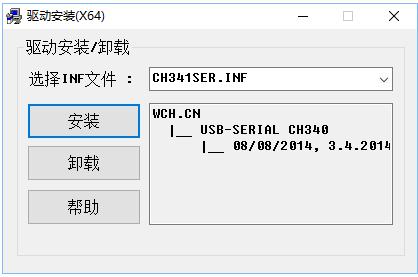
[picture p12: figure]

驱动安装成功后，在设备管理器可以看到会有一个端口出现。

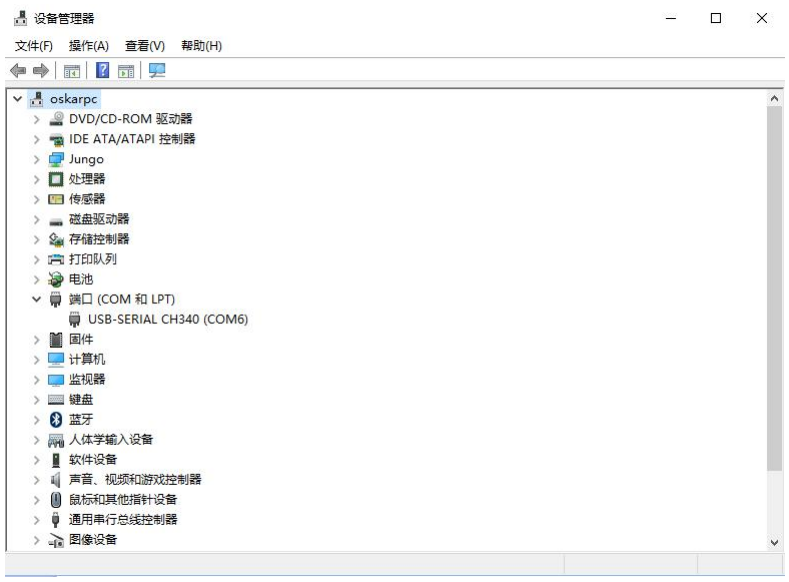
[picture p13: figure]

如果驱动已经安装过，但对应端口旁有叹号提示，可以右击更新驱动，然后浏览已经安装好

的驱动，选择正确驱动即可，如下图。

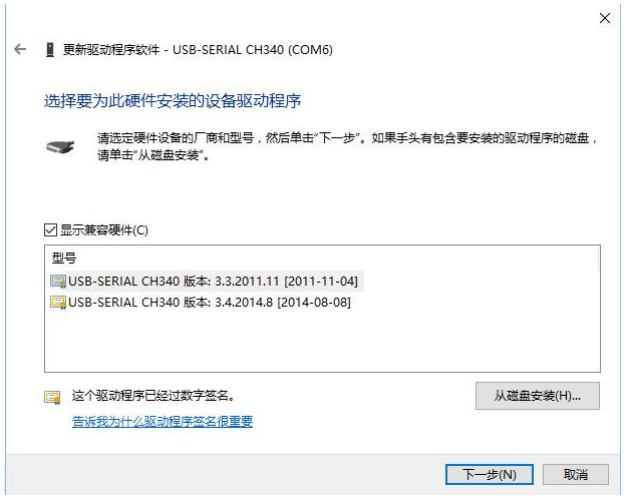
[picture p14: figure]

### 6.2 烧录固件

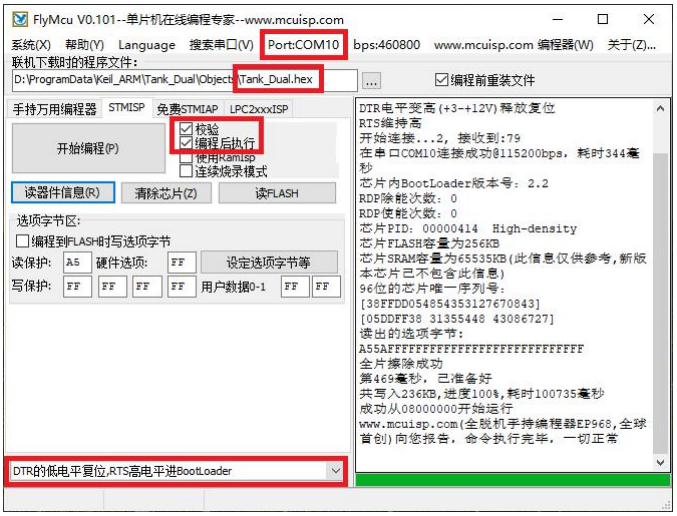
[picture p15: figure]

操作流程：

1、用miniUSB线将手柄连接到电脑上，选择正确的端口，这里是COM10，波特率115200. 如果不确定是哪个端口，可以打开设备管理器查看。如果没有找到对应端口，请检查驱动程

序是否安装正确，驱动安装见上一章节。

2、浏览到需要升级的固件（hex）文件。

3、选择 STMISP，然后勾选“校验”和“编程后执行”。

4、选择“DTR 的低电平复位，RTS 高电平进 BootLoader”。

5、用手按住手柄上的电源键“P3 键”不要松开，点击“开始编程”，直到程序下载完成。

控制板升级固件后，无线配置全部恢复默认设置。

### 7、尺寸说明

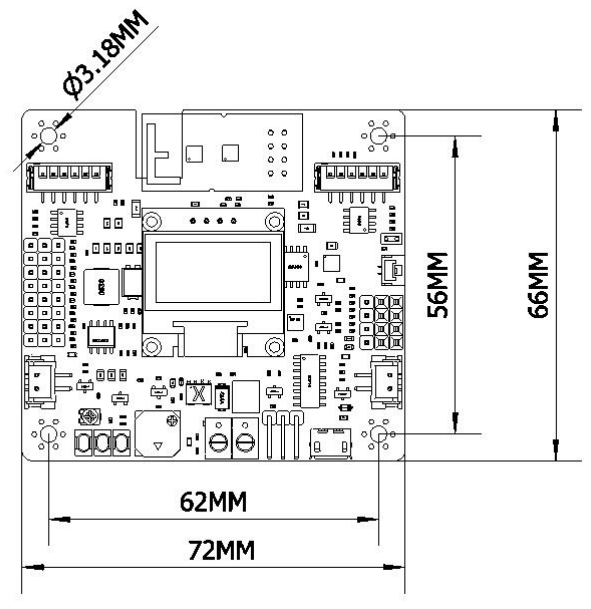
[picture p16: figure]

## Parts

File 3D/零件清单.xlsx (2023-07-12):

序号 | 名称 | 规格 | 采购链接
1 | STM32控制板 | 控制板+手柄+电池套装 | https://item.taobao.com/item.htm?id=565040857054
2 | 直流有刷减速电机（带编码器） | 12V333转每分钟，霍尔正交编码器，注意接口线序要和控制板一致 | https://item.taobao.com/item.htm?id=568891885142
3 | 传动皮带轮 | 40齿内孔12mm（带宽6mm） | https://item.taobao.com/item.htm?spm=a1z09.2.0.0.32ef2e8dUheqov&id=528687341718&_u=bp7475654d7
4 | 大轴承 | 6704ZZ 20*27*4（mm） | https://item.taobao.com/item.htm?spm=a1z09.2.0.0.32ef2e8dUheqov&id=22147131905&_u=bp74756851f
5 | 小轴承 | mr128zz 8*12*3.5（mm） | https://item.taobao.com/item.htm?spm=a1z09.2.0.0.32ef2e8dUheqov&id=25978636578&_u=bp747560fd6
6 | 2GT环形同步带 | 周长286-332mm 宽度：6mm | https://item.taobao.com/item.htm?spm=a1z09.2.0.0.32ef2e8d7mT10k&id=677341747083&_u=bp747568acc
7 | 螺丝螺母 | M3螺丝长度10毫米和12毫米的若干，螺母若干
8 | 铜柱 | M3铜柱，长度50到60毫米

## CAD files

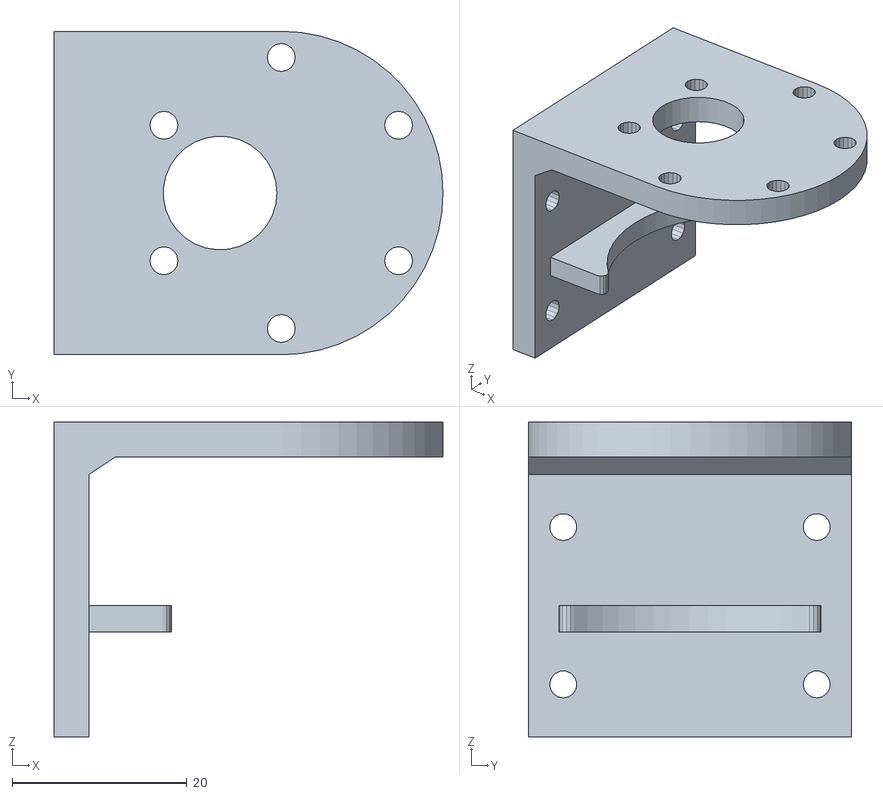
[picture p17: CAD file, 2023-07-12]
3D/4_电机支架.stl
44.5 x 37.0 x 36.0

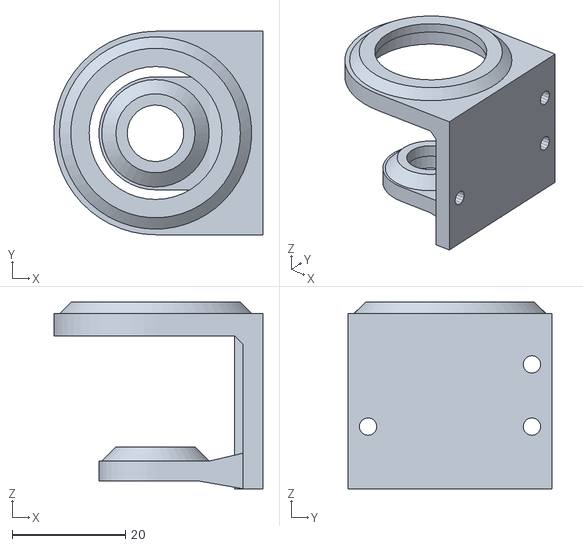
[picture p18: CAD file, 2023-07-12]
3D/5_从动轮支架.stl
37.0 x 36.0 x 33.0

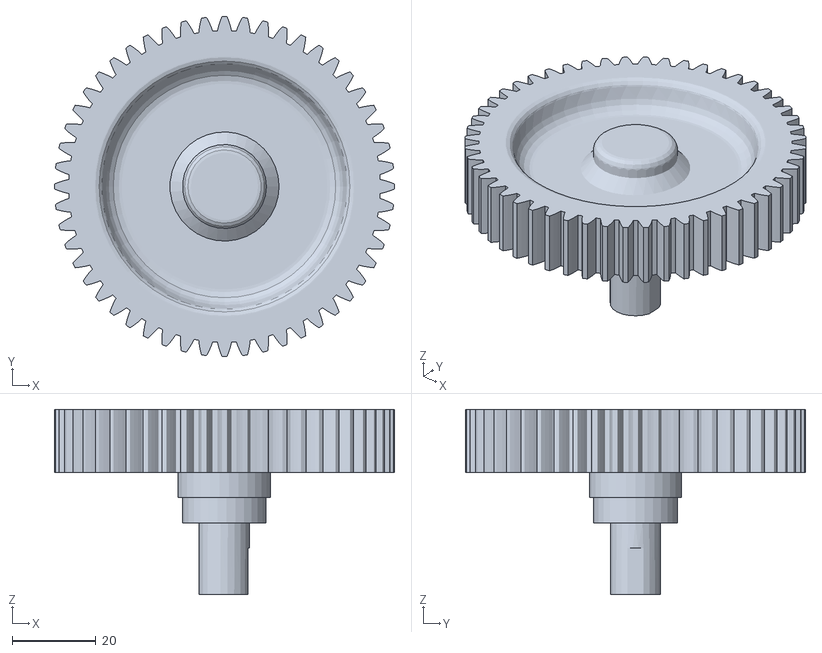
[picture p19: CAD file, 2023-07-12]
3D/1_主动轮.stl
81.0 x 81.0 x 44.1

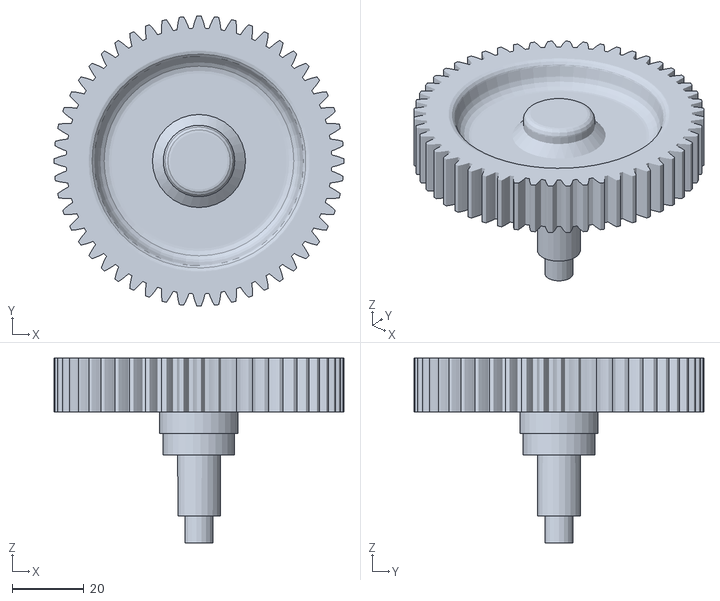
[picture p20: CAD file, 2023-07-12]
3D/2_从动轮.stl
81.0 x 81.0 x 51.6

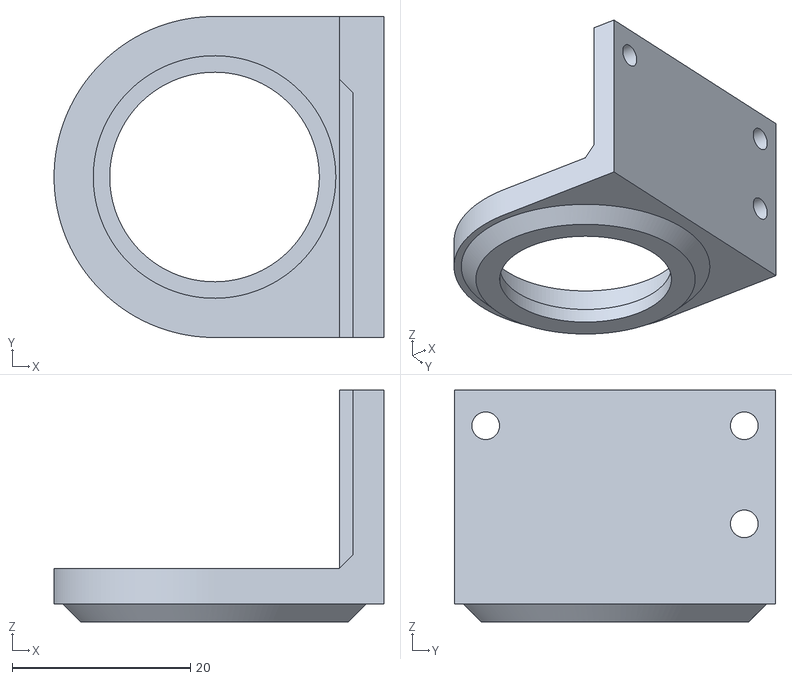
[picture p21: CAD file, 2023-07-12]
3D/3_主动轮支架.stl
37.0 x 36.0 x 26.0

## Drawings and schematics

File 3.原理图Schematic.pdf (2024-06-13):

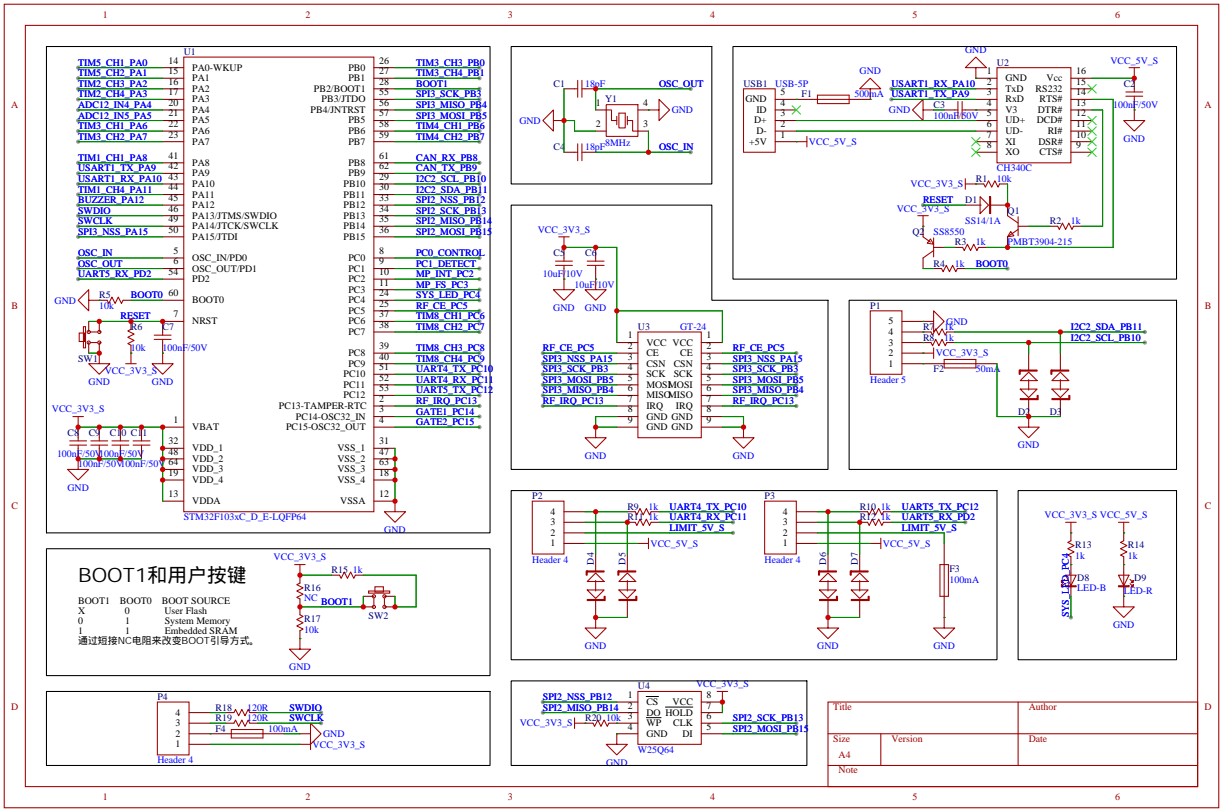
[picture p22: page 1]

# PWM接口

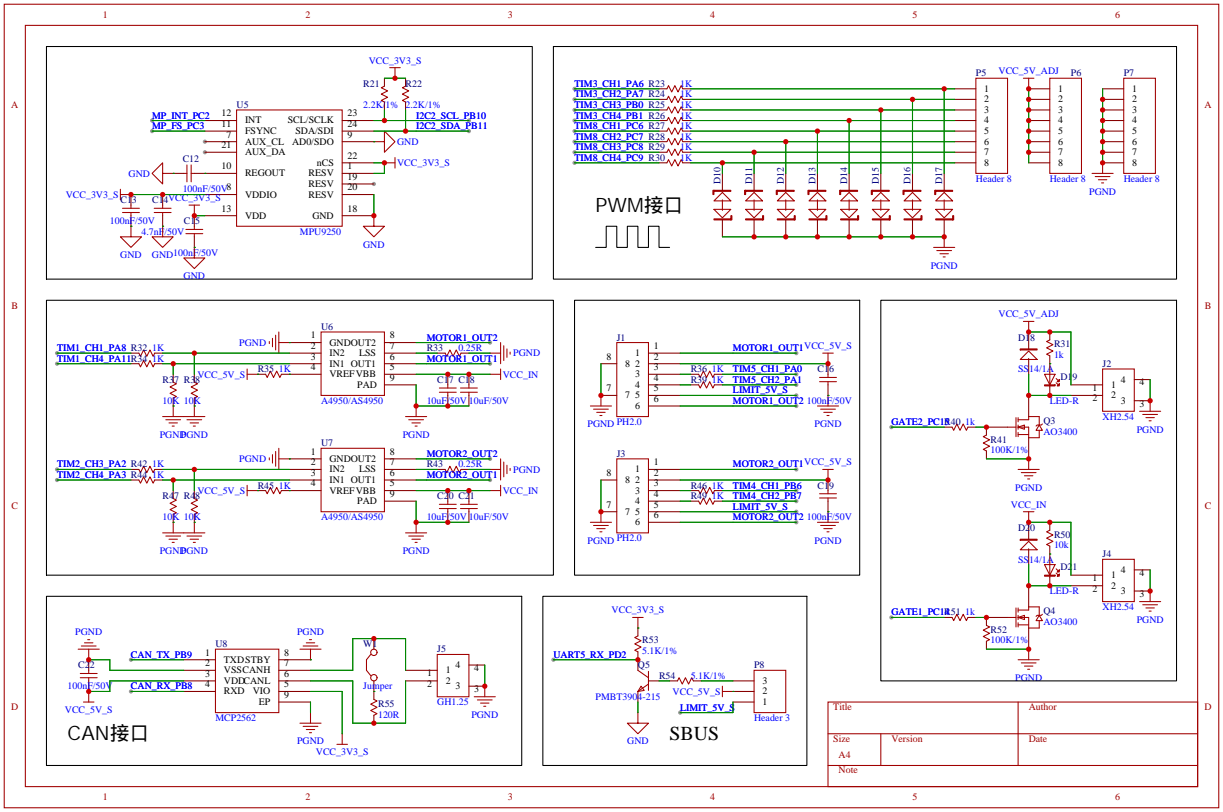
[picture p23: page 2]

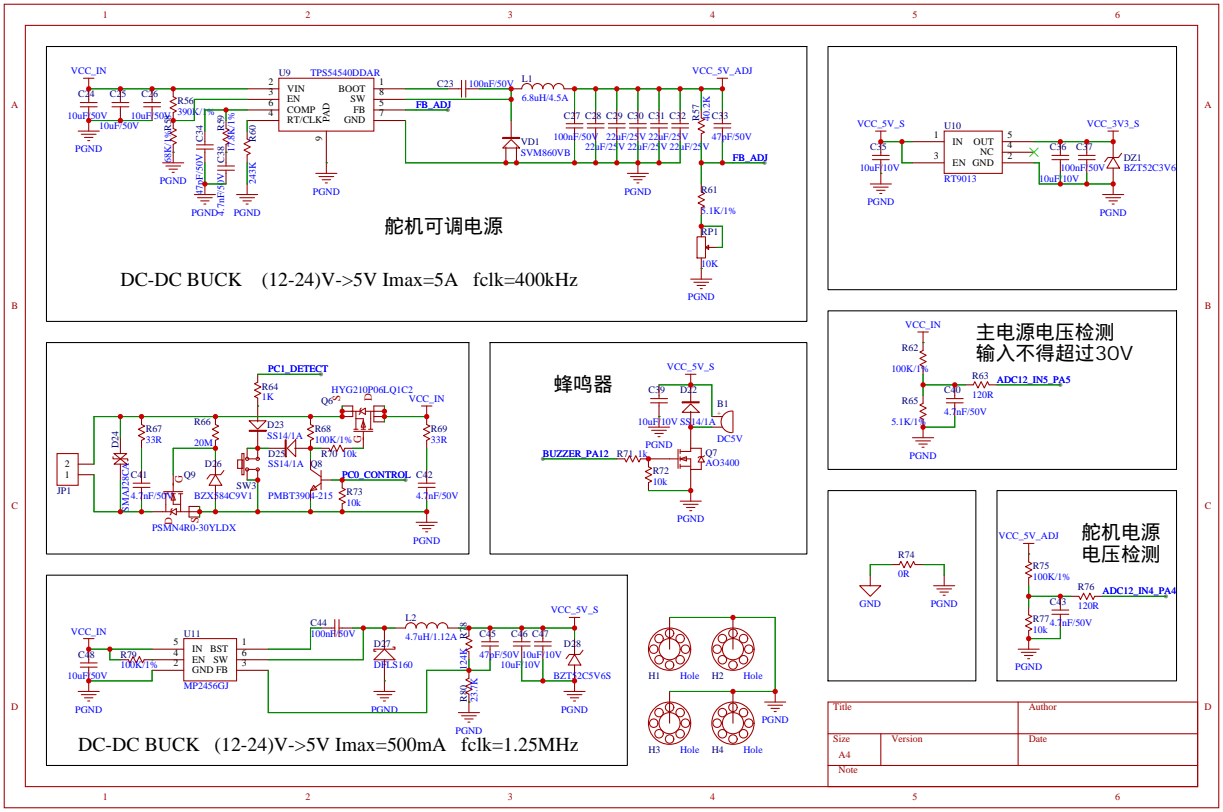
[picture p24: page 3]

DC-DC BUCK (12-24)V->5V Imax=5A fclk=400kHz

PGND
DC-DC BUCK (12-24)V->5V Imax=500mA fclk=1.25MHz

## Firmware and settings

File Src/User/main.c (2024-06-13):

/**
  ******************************************************************************
  * @file    main.c
  * @author: Oskar Wei
  * @version 2.1
  * @date    2020-05-17
  * @brief   Main program body
  ******************************************************************************
  * @attention
  *
  * Mail: 990092230@qq.com
  * Shop: www.mindsilicon.com
  *
	* 该程序仅供学习使用，未经作者允许，不得用于其它任何用途
  ******************************************************************************
  */

/* Includes ------------------------------------------------------------------*/
#include "stm32f10x.h"
#include "stm32f10x_it.h"
#include <stdio.h>
#include "led.h"
#include "usart1.h"
#include "uart4.h"
#include "uart5.h"
#include "spi_flash.h"
#include "ff.h"
#include "string.h"
#include "key.h"
#include "i2c_oled.h"
#include "delay.h"
#include "buzzer.h"
#include "watchdog.h"
#include "delay.h"
#include "sensors.h"
#include "utils.h"
#include "power_control.h"
#include "adc.h"
#include "can.h"
#include "servo.h"
#include "motor.h"
#include "radio.h"
#include "flash.h"

#include "FreeRTOS.h"	// 此处"x"提示,是因为IDE误报,与代码无关，没有影响
#include "task.h"

#include "i2c_device.h"

/* Private define ------------------------------------------------------------*/
/* Extern define ------------------------------------------------------------*/
/* Private macro -------------------------------------------------------------*/
/* Private variables ---------------------------------------------------------*/
/* Private function prototypes -----------------------------------------------*/
/* Private functions ---------------------------------------------------------*/




TaskHandle_t startTaskHandle;
extern xTaskHandle radiolinkTaskHandle;

static void startTask(void *arg);

uint8_t can_buf[8] = {'H','i','!','C','A','N','!','\n'};

int main(void)
{
	// 中断优先级分组配置
	NVIC_PriorityGroupConfig(NVIC_PriorityGroup_4);
	
	// 延时初始化
	Delay_Init(72);
	
	// 用户键初始化
	UserKey_Init();
	
	LED_Init();

	USART1_Init(115200);
	printf("Hello  world !\r\n");
	UART4_Init(9600);
	UART5_Init(9600);
	
	i2cdevInit(I2C2_DEV);
	
	// 加载STM32片内Flash存储器中保存的配置数据,包括地址、频率、摇杆校准数据
	LoadConfigData();
	
	FileSystem_Init();
	
	ADCx_Init();
	
	Servo_Init();
	
	CAN_Mode_Init(CAN_SJW_1tq,CAN_BS1_4tq,CAN_BS1_4tq,4,CAN_Mode_Normal);//CAN初始化环回模式,波特率1Mbps
		
	// 初始化看门狗
	watchdogInit(WATCHDOG_RELOAD_MS);
	
	xTaskCreate(startTask, "START_TASK", 300, NULL, 1, &startTaskHandle);	/*创建起始任务*/

	vTaskStartScheduler();	/*开启任务调度*/
	
	
	/* 不再使用文件系统,取消挂载文件系统 */
	f_mount(NULL,"1:",1);
	LED_TOGGLE;
}


// 创建任务
void startTask(void *arg)
{
	// 进入临界区
	taskENTER_CRITICAL();
	
	printf("Free heap before starting: %d bytes\n", xPortGetFreeHeapSize());
	
	xTaskCreate(SensorTask, "SENSORS", 300, NULL, 5, NULL);			        /*创建传感器处理任务*/

	xTaskCreate(MenuTask, "MENU", 1550, NULL, 4, NULL);						/*创建显示处理任务*/
	
	xTaskCreate(PlayMusic, "PlayMusic", 100, NULL, 4, NULL);			       /*创建音乐处理任务*/
	
	xTaskCreate(PowerTask, "POWER", 50, NULL, 4, NULL);
	
	xTaskCreate(MotorTask, "MOTOR", 100, NULL, 5, NULL);
	
	xTaskCreate(RadioTask, "RADIO", 100, NULL, 5, NULL);

	xTaskCreate(Usart1Task, "USART1", 100, NULL, 4, NULL);
	
	xTaskCreate(Uart4Task, "UART4", 150, NULL, 4, NULL);
	
	xTaskCreate(Uart5Task, "UART5", 100, NULL, 4, NULL);
	
	// 打印剩余堆栈大小
	printf("Free heap after starting: %d bytes\n", xPortGetFreeHeapSize());
	
	// 删除开始任务
	vTaskDelete(startTaskHandle);
	
	// 退出临界区
	taskEXIT_CRITICAL();
} 




// 空闲任务,CPU空闲时执行
void vApplicationIdleHook( void )
{
//	static char pWriteBuffer[1124];

	watchdogReset();
	
//	vTaskList((char *)&pWriteBuffer);
//	printf("task_name   state   priority   stack   num\n");
//	printf("%s\n", pWriteBuffer);
	
//	CanSendMsg(can_buf,8);//发送8个字节
	
//	__WFI();	/*进入低功耗模式*/
}





void vApplicationMallocFailedHook( void )
{
	portDISABLE_INTERRUPTS();
	printf("\nMalloc failed!\n");
	LED_TOGGLE;
	while(1);
}

#if (configCHECK_FOR_STACK_OVERFLOW == 1)
void vApplicationStackOverflowHook(xTaskHandle *pxTask, signed portCHAR *pcTaskName)
{
	portDISABLE_INTERRUPTS();
	printf("\nStack overflow!\n");
	LED_TOGGLE;
	while(1);
}
#endif








#ifdef  USE_FULL_ASSERT

/**
  * @brief  Reports the name of the source file and the source line number
  *         where the assert_param error has occurred.
  * @param  file: pointer to the source file name
  * @param  line: assert_param error line source number
  * @retval None
  */
void assert_failed(uint8_t* file, uint32_t line)
{ 
  /* User can add his own implementation to report the file name and line number,
     ex: printf("Wrong parameters value: file %s on line %d\r\n", file, line) */

  /* Infinite loop */
  while (1)
  {
  }
}
#endif

/**
  * @}
  */


/******************* (C) COPYRIGHT 2011 STMicroelectronics *****END OF FILE****/

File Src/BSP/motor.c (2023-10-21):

/**
  ******************************************************************************
  * @file    motor.c
  * @author  Oskar Wei
  * @version V1.0
  * @date    2020-06-06
  * @brief   motor control api
  ******************************************************************************
  * @attention
  *
  * Mail: 990092230@qq.com
  * Blog: www.mindsilicon.com
  *
	* 该程序仅供学习使用，未经作者允许，不得用于其它任何用途
  ******************************************************************************
  */
	
#include "can.h"
#include "radio.h"
#include "motor.h"
#include "i2c_oled.h"
#include "usart1.h"
#include "stdio.h"
#include "stm32f10x_it.h"

#include "FreeRTOS.h"
#include "task.h"

extern Menu menu;
extern servoPWM_t servoPWM;

motorStatus_t motorStatus = 
{
	.motor1_pwm = 0,					// 电机1PWM值
	.motor2_pwm = 0,					// 电机2PWM值
	.target_speed1 = 0,				// 电机1目标速度,毫米每秒,最高2位含义为, 二进制00:惯性滑行,01:正转,10:反转,11:阻尼刹车,详情参考手册中通信协议部分
	.target_speed2 = 0,				// 电机2目标速度,毫米每秒,最高2位含义为, 二进制00:惯性滑行,01:正转,10:反转,11:阻尼刹车,详情参考手册中通信协议部分
	.current_speed1 = 0,			// 电机1当前速度,毫米每秒,最高2位含义为, 二进制00:惯性滑行,01:正转,10:反转,11:阻尼刹车,详情参考手册中通信协议部分
	.current_speed2 = 0,			// 电机2当前速度,毫米每秒,最高2位含义为, 二进制00:惯性滑行,01:正转,10:反转,11:阻尼刹车,详情参考手册中通信协议部分
	.motor1_pulse = 0,				// 电机1编码器在上一个时间片内的脉冲数,即当前脉冲数,每两次采样之间的时间称为1个时间片
	.motor2_pulse = 0,				// 电机1编码器在上一个时间片内的脉冲数,即当前脉冲数,每两次采样之间的时间称为1个时间片
	.motor1_pulse_total = 0,	// 电机1脉冲总计
	.motor2_pulse_total = 0,	// 电机2脉冲总计
	.motor1_status = 0, 			// 电机1状态,0:正常,1:编码器异常
	.motor2_status = 0  			// 电机2状态,0:正常,1:编码器异常
};



// 初始化用于驱动电机1的定时器，以便向A4950电机驱动芯片输出合适的PWM信号
void TIM1_Init(void)
{
	GPIO_InitTypeDef GPIO_InitStructure;
	TIM_TimeBaseInitTypeDef  TIM_TimeBaseStructure;

	// 输出比较通道GPIO 初始化
	RCC_APB2PeriphClockCmd(RCC_APB2Periph_GPIOA | RCC_APB2Periph_TIM1, ENABLE);
	GPIO_InitStructure.GPIO_Pin =  GPIO_Pin_8 | GPIO_Pin_11;
	GPIO_InitStructure.GPIO_Mode = GPIO_Mode_AF_PP;
	GPIO_InitStructure.GPIO_Speed = GPIO_Speed_50MHz;
	GPIO_Init(GPIOA, &GPIO_InitStructure);
	
	/*--------------------时基结构体初始化-------------------------*/
	// 配置周期，这里配置为1ms
	
	// 自动重装载寄存器的值，累计TIM_Period+1个频率后产生一个更新或者中断
	TIM_TimeBaseStructure.TIM_Period = MOTOR_PWM_RESOLUTION;	
	// 驱动CNT计数器的时钟 = Fck_int/(psc+1)
	TIM_TimeBaseStructure.TIM_Prescaler = MOTOR_TIM_PSC_APB1;	
	// 时钟分频因子，配置死区时间时需要用到
	TIM_TimeBaseStructure.TIM_ClockDivision=TIM_CKD_DIV1;		
	// 计数器计数模式，设置为向上计数
	TIM_TimeBaseStructure.TIM_CounterMode=TIM_CounterMode_Up;		
	// 重复计数器的值，没用到不用管
	TIM_TimeBaseStructure.TIM_RepetitionCounter=0;	
	// 初始化定时器
	TIM_TimeBaseInit(TIM1, &TIM_TimeBaseStructure);
	
	/*--------------------输出比较结构体初始化-------------------*/

	TIM_OCInitTypeDef  TIM_OCInitStructure;
	// 配置为PWM模式1
	TIM_OCInitStructure.TIM_OCMode = TIM_OCMode_PWM1;
	// 输出使能
	TIM_OCInitStructure.TIM_OutputState = TIM_OutputState_Enable;
	// 输出通道电平极性配置
	TIM_OCInitStructure.TIM_OCPolarity = TIM_OCPolarity_High;
	
	// 输出比较通道 1
	TIM_OCInitStructure.TIM_Pulse = MOTOR_DEFAULT_DUTY;
	TIM_OC1Init(TIM1, &TIM_OCInitStructure);
	TIM_OC1PreloadConfig(TIM1, TIM_OCPreload_Enable);
	
	// 输出比较通道 4
	TIM_OCInitStructure.TIM_Pulse = MOTOR_DEFAULT_DUTY;
	TIM_OC4Init(TIM1, &TIM_OCInitStructure);
	TIM_OC4PreloadConfig(TIM1, TIM_OCPreload_Enable);
	
	//TIM_ARRPreloadConfig(TIM1, ENABLE);
	// 使能计数器
	TIM_Cmd(TIM1, ENABLE);
	
	// 主输出使能，当使用的是通用定时器时，这句不需要
	TIM_CtrlPWMOutputs(TIM1, ENABLE);
}



// 初始化用于驱动电机2的定时器，以便向A4950电机驱动芯片输出合适的PWM信号
void TIM2_Init(void)
{
	GPIO_InitTypeDef GPIO_InitStructure;
	TIM_TimeBaseInitTypeDef  TIM_TimeBaseStructure;
	
	// 输出比较通道GPIO 初始化
	RCC_APB2PeriphClockCmd(RCC_APB2Periph_GPIOA, ENABLE);
	GPIO_InitStructure.GPIO_Pin =  GPIO_Pin_2 | GPIO_Pin_3;
	GPIO_InitStructure.GPIO_Mode = GPIO_Mode_AF_PP;
	GPIO_InitStructure.GPIO_Speed = GPIO_Speed_50MHz;
	GPIO_Init(GPIOA, &GPIO_InitStructure);
	
	// 开启定时器时钟
	RCC_APB1PeriphClockCmd(RCC_APB1Periph_TIM2, ENABLE);
	
	/*--------------------时基结构体初始化-------------------------*/
	// 配置周期，这里配置为1ms

	// 自动重装载寄存器的值，累计TIM_Period+1个频率后产生一个更新或者中断
	TIM_TimeBaseStructure.TIM_Period = MOTOR_PWM_RESOLUTION;	
	// 驱动CNT计数器的时钟 = Fck_int/(psc+1)
	TIM_TimeBaseStructure.TIM_Prescaler = MOTOR_TIM_PSC_APB1;	
	// 时钟分频因子，配置死区时间时需要用到
	TIM_TimeBaseStructure.TIM_ClockDivision=TIM_CKD_DIV1;		
	// 计数器计数模式，设置为向上计数
	TIM_TimeBaseStructure.TIM_CounterMode=TIM_CounterMode_Up;		
	// 重复计数器的值，没用到不用管
	TIM_TimeBaseStructure.TIM_RepetitionCounter=0;	
	// 初始化定时器
	TIM_TimeBaseInit(TIM2, &TIM_TimeBaseStructure);
	
	/*--------------------输出比较结构体初始化-------------------*/

	TIM_OCInitTypeDef  TIM_OCInitStructure;
	// 配置为PWM模式1
	TIM_OCInitStructure.TIM_OCMode = TIM_OCMode_PWM1;
	// 输出使能
	TIM_OCInitStructure.TIM_OutputState = TIM_OutputState_Enable;
	// 输出通道电平极性配置
	TIM_OCInitStructure.TIM_OCPolarity = TIM_OCPolarity_High;
	
	// 输出比较通道 3
	TIM_OCInitStructure.TIM_Pulse = MOTOR_DEFAULT_DUTY;
	TIM_OC3Init(TIM2, &TIM_OCInitStructure);
	TIM_OC3PreloadConfig(TIM2, TIM_OCPreload_Enable);
	
	// 输出比较通道 4
	TIM_OCInitStructure.TIM_Pulse = MOTOR_DEFAULT_DUTY;
	TIM_OC4Init(TIM2, &TIM_OCInitStructure);
	TIM_OC4PreloadConfig(TIM2, TIM_OCPreload_Enable);
	
	//TIM_ARRPreloadConfig(TIM2, ENABLE);
	
	// 使能计数器
	TIM_Cmd(TIM2, ENABLE);
}


// 初始化电机1的编码器,这里用了TIM5
void Motor1_Encoder_Init(void)
{
	TIM_TimeBaseInitTypeDef TIM_TimeBaseStructure;  
  TIM_ICInitTypeDef TIM_ICInitStructure;  
  GPIO_InitTypeDef GPIO_InitStructure;
  RCC_APB1PeriphClockCmd(RCC_APB1Periph_TIM5, ENABLE);	// 使能定时器5的时钟
	
	/*使能GPIOA和AFIO外设时钟*/
	RCC_APB2PeriphClockCmd(RCC_APB2Periph_GPIOA | RCC_APB2Periph_AFIO, ENABLE);
	
	/*初始化PA0和PA1端口为IN_FLOATING模式*/
	GPIO_InitStructure.GPIO_Pin = GPIO_Pin_0 | GPIO_Pin_1;
	GPIO_InitStructure.GPIO_Mode = GPIO_Mode_IN_FLOATING;
	GPIO_Init(GPIOA, &GPIO_InitStructure);
	
  TIM_TimeBaseStructInit(&TIM_TimeBaseStructure);
  TIM_TimeBaseStructure.TIM_Prescaler = 0;			// 预分频器
  TIM_TimeBaseStructure.TIM_Period = 0xFFFF;		// 设定计数器自动重装值
  TIM_TimeBaseStructure.TIM_ClockDivision = TIM_CKD_DIV1;				// 选择时钟分频：不分频
  TIM_TimeBaseStructure.TIM_CounterMode = TIM_CounterMode_Up;		// TIM向上计数
  TIM_TimeBaseInit(TIM5, &TIM_TimeBaseStructure);
  TIM_EncoderInterfaceConfig(TIM5, TIM_EncoderMode_TI12, TIM_ICPolarity_Rising, TIM_ICPolarity_Rising);	// 使用编码器模式
	
	TIM_ICStructInit(&TIM_ICInitStructure);
	TIM_ICInitStructure.TIM_ICFilter = 10;
	TIM_ICInit(TIM5, &TIM_ICInitStructure);
	
  TIM_ClearFlag(TIM5, TIM_FLAG_Update);				// 清除TIM的更新标志位
  TIM_ITConfig(TIM5, TIM_IT_Update, ENABLE);
	
  TIM_SetCounter(TIM5, 0);		// 清除计数器
  TIM_Cmd(TIM5, ENABLE); 
}
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

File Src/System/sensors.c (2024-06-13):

/**
  ******************************************************************************
  * @file    sensor.c
  * @author: Oskar Wei
	* @Mail:   990092230@qq.com
  * @version 1.1
  * @date    2020-05-17
  * @brief   sensor top level api
  ******************************************************************************
  * @attention
  *
  * COPYRIGHT Oskarbot 2020
  ******************************************************************************
  */ 


#include <math.h>
#include "stdio.h"
#include "delay.h"
#include "filter.h"
#include "mpu9250.h"
#include "sensors.h"
#include "ak8963.h"
#include "led.h"
#include "i2c_oled.h"
#include "stm32f10x_it.h"
#include "ekf.h"
#include "radio.h"


/*FreeRTOS相关头文件*/
#include "FreeRTOS.h"
#include "task.h"



#define SENSORS_GYRO_FS_CFG       MPU6500_GYRO_FS_2000
#define SENSORS_DEG_PER_LSB_CFG   MPU6500_DEG_PER_LSB_2000

#define SENSORS_ACCEL_FS_CFG      MPU6500_ACCEL_FS_2	
#define SENSORS_G_PER_LSB_CFG     MPU6500_G_PER_LSB_2

#define SENSORS_NBR_OF_BIAS_SAMPLES		1024	/* 计算方差的采样样本个数 */
#define GYRO_VARIANCE_BASE				4000	/* 陀螺仪零偏方差阈值 */
#define SENSORS_ACC_SCALE_SAMPLES  		200		/* 加速计采样个数 */

// MPU9250主机模式读取数据 缓冲区长度
#define SENSORS_MPU6500_BUFF_LEN    14
#define SENSORS_MAG_BUFF_LEN       	8

typedef struct
{
	Axis3f     bias;
	bool       isBiasValueFound;
	bool       isBufferFilled;
	Axis3i16*  bufHead;
	Axis3i16   buffer[SENSORS_NBR_OF_BIAS_SAMPLES];
}BiasObj;

BiasObj	gyroBiasRunning;
static Axis3f  gyroBias;

static bool gyroBiasFound = false;
static float accScaleSum = 0;
static float accScale = 1;

static bool isInit = false;
sensorData_t sensors;
state_t state;		/*四轴姿态*/
static int8_t AK8963_ASA[3];

static Axis3i16	gyroRaw;
static Axis3i16	accRaw;
static Axis3i16 magRaw;

/*低通滤波参数*/
#define GYRO_LPF_CUTOFF_FREQ  80
#define ACCEL_LPF_CUTOFF_FREQ 30
static lpf2pData accLpf[3];
static lpf2pData gyroLpf[3];

static bool isMPUPresent=false;
static bool isMagPresent=false;

static uint8_t buffer[SENSORS_MPU6500_BUFF_LEN + SENSORS_MAG_BUFF_LEN] = {0};

static xQueueHandle accelerometerDataQueue;
static xQueueHandle gyroDataQueue;
static xQueueHandle magnetometerDataQueue;
static xSemaphoreHandle sensorsDataReady;


void applyAxis3fLpf(lpf2pData *data, Axis3f* in);
void sensorsBiasObjInit(BiasObj* bias);
void sensorsCalculateVarianceAndMean(BiasObj* bias, Axis3f* varOut, Axis3f* meanOut);
bool sensorsFindBiasValue(BiasObj* bias);
void sensorsAddBiasValue(BiasObj* bias, int16_t x, int16_t y, int16_t z);


/*从队列读取陀螺数据*/
bool sensorsReadGyro(Axis3f *gyro)
{
	return (pdTRUE == xQueueReceive(gyroDataQueue, gyro, 0));
	
//	if(pdTRUE == xQueueReceive(gyroDataQueue, gyro, 0))
//	{
//		printf("\n(pdTRUE == xQueueReceive(gyroDataQueue, gyro, 0)   success\n");
//	}
//	else
//	{
//		printf("\n(pdTRUE == xQueueReceive(gyroDataQueue, gyro, 0)   failed\n");
//	}
//	
	
	
}
/*从队列读取加速计数据*/
bool sensorsReadAcc(Axis3f *acc)
{
	return (pdTRUE == xQueueReceive(accelerometerDataQueue, acc, 0));
}
/*从队列读取磁力计数据*/
bool sensorsReadMag(Axis3f *mag)
{
	return (pdTRUE == xQueueReceive(magnetometerDataQueue, mag, 0));
}

/*传感器中断初始化*/
void sensorsInterruptInit(void)
{
	GPIO_InitTypeDef GPIO_InitStructure;
	EXTI_InitTypeDef EXTI_InitStructure;
	NVIC_InitTypeDef NVIC_InitStructure;
	
		/*使能GPIOD、AFIO外设时钟*/
	RCC_APB2PeriphClockCmd(RCC_APB2Periph_GPIOC | RCC_APB2Periph_AFIO, ENABLE);

	/*使能MPU6500中断*/
	GPIO_InitStructure.GPIO_Pin = GPIO_Pin_2;
	GPIO_InitStructure.GPIO_Mode = GPIO_Mode_IPD;
	GPIO_InitStructure.GPIO_Speed = GPIO_Speed_50MHz; 
	GPIO_Init(GPIOC, &GPIO_InitStructure);
	
	
	GPIO_EXTILineConfig(GPIO_PortSourceGPIOC, GPIO_PinSource2);
	EXTI_InitStructure.EXTI_Line = EXTI_Line2;
	EXTI_InitStructure.EXTI_Mode = EXTI_Mode_Interrupt;
	EXTI_InitStructure.EXTI_Trigger = EXTI_Trigger_Rising;
	EXTI_InitStructure.EXTI_LineCmd = ENABLE;
	portDISABLE_INTERRUPTS();
	EXTI_Init(&EXTI_InitStructure);
	EXTI_ClearITPendingBit(EXTI_Line2);
	portENABLE_INTERRUPTS();
	
	NVIC_InitStructure.NVIC_IRQChannel = EXTI2_IRQn;
  NVIC_InitStructure.NVIC_IRQChannelPreemptionPriority = 6;
  NVIC_InitStructure.NVIC_IRQChannelSubPriority = 0;
  NVIC_InitStructure.NVIC_IRQChannelCmd = ENABLE;
  NVIC_Init(&NVIC_InitStructure);
}

/* 传感器器件初始化 */
void sensorsDeviceInit(void)
{
//	int8_t asa[3] = {0};
//	i2cdevInit(I2C2_DEV);
	mpu6500Init(I2C2_DEV);
	vTaskDelay(10);
	
	mpu6500Reset();	// 复位MPU6500
	
	vTaskDelay(20);	// 延时等待寄存器复位
	
	u8 temp = mpu6500GetDeviceID();
	
	// MPU6500 Chip ID: 0x71
	if (temp == 0x71)
	{
		isMPUPresent=true;
		printf("MPU6500 I2C connection [OK].\n");
	}
	else
	{
		printf("MPU6500 I2C connection [FAIL].\n");
	}
	
	mpu6500SetSleepEnabled(false);												// 唤醒MPU6500
	vTaskDelay(10);		
	mpu6500SetClockSource(MPU6500_CLOCK_PLL_XGYRO);				// 设置X轴陀螺作为时钟
	vTaskDelay(10);																				// 延时等待时钟稳定
	mpu6500SetTempSensorEnabled(true);										// 使能温度传感器
	mpu6500SetIntEnabled(false);													// 关闭中断
	mpu6500SetI2CBypassEnabled(true);											// 旁路模式，磁力计和气压连接到主IIC
	mpu6500SetFullScaleGyroRange(SENSORS_GYRO_FS_CFG);		// 设置陀螺量程, 2000°/s
	mpu6500SetFullScaleAccelRange(SENSORS_ACCEL_FS_CFG);	// 设置加速计量程, 2G
	mpu6500SetAccelDLPF(MPU9250_ACCEL_DLPF_BW_45);				// 设置加速计数字低通滤波

//	mpu6500SetRate(0);// 设置采样速率: 1000 / (1 + 0) = 1000Hz
	mpu6500SetRate(4);																		// 设置采样速率: 1000 / (1 + 4) = 200Hz
	mpu6500SetDLPFMode(MPU9250_GYRO_DLPF_BW_92);					// 设置陀螺数字低通滤波
	
	for (uint8_t i = 0; i < 3; i++)												// 初始化加速计和陀螺二阶低通滤波
	{
		lpf2pInit(&gyroLpf[i], 1000, GYRO_LPF_CUTOFF_FREQ);
		lpf2pInit(&accLpf[i],  1000, ACCEL_LPF_CUTOFF_FREQ);
	}
	
#ifdef SENSORS_ENABLE_MAG_AK8963
	ak8963Init(I2C2_DEV);	//ak8963磁力计初始化
	if (ak8963TestConnection() == true)
	{
		isMagPresent = true;
		ak8963SetMode(AK8963_MODE_16BIT | AK8963_MODE_CONT2); // 16bit 100Hz
//		ak8963GetAdjustment(&asa[0], &asa[1], &asa[2]);
//		AK8963_ASA[0] = (int16_t)asa[0] + 128;
//		AK8963_ASA[1] = (int16_t)asa[1] + 128;
//		AK8963_ASA[2] = (int16_t)asa[2] + 128;
		
		printf("AK8963 I2C connection [OK].\n");
	}
	else
	{
		printf("AK8963 I2C connection [FAIL].\n");
	}
#endif

	/*创建传感器数据队列*/
	accelerometerDataQueue = xQueueCreate(1, sizeof(Axis3f));
	gyroDataQueue = xQueueCreate(1, sizeof(Axis3f));
	magnetometerDataQueue = xQueueCreate(1, sizeof(Axis3f));
}
/*传感器偏置初始化*/
void sensorsBiasObjInit(BiasObj* bias)
{
	bias->isBufferFilled = false;
	bias->bufHead = bias->buffer;
}
/*传感器测试*/
bool sensorsTest(void)
{
	bool testStatus = true;

	if (!isInit)
	{
		printf("Uninitialized\n");
		testStatus = false;
	}
	
	return testStatus;
}
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

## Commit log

2022-11-08 新建 image
2022-11-08 删除文件 imageimage.png
2022-11-08 删除文件 image3.png
2022-11-08 删除文件 image2.png
2023-06-03 Modified Schematic
2023-07-12 upload 3D model
    [1_主动轮.stl, 2_从动轮.stl, 3_主动轮支架.stl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]
2023-10-20 support gcc printf on usart1
2023-10-21 fix some bugs on gcc compiler
    [buzzer.c, main.c, motor.c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]
2023-10-21 fix some warnings on gcc compiler
    [usart1.c]
2024-06-13 Modified the parameters of some devices in the schematic
